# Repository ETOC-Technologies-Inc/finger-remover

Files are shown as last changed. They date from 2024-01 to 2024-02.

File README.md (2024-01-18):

# finger-remover
Tool for cutting velcro - our latest and greatest in finger removing technology

Pretty simple hardware wise (complete lies), you only need a few other (lie) parts apart from a few (lie) the 3D printed parts:
* Arduino Leonardo
* Two MG995 or One MG995 and One DS3218MG
* One Encoder without a button (i used KLS4-EC1101-5A-F20) and one Encoder module with a button (like whatever adafruit sells)
* 

# TODO/Issues

1) Fix feeding issues, oh yeah the velcro is not feeding properly rn :)

2) Add a casing for electronics, it would be nice to not hold the mess of wires in my hands

3) Make a PCB hat for the arduino its based on, and maybe add an proper LDO to it, the wires are a fucking mess and i hate them

4) Make the servo mounts fit the servos a bit less tight? They are almost impossible to slot into the mounts without a hammer rn

# Contributions

Open an issue in this repo if you see something wrong, open an MR if you think you have a fix for it, other than that pretty much anything that comlies with the license is fine.

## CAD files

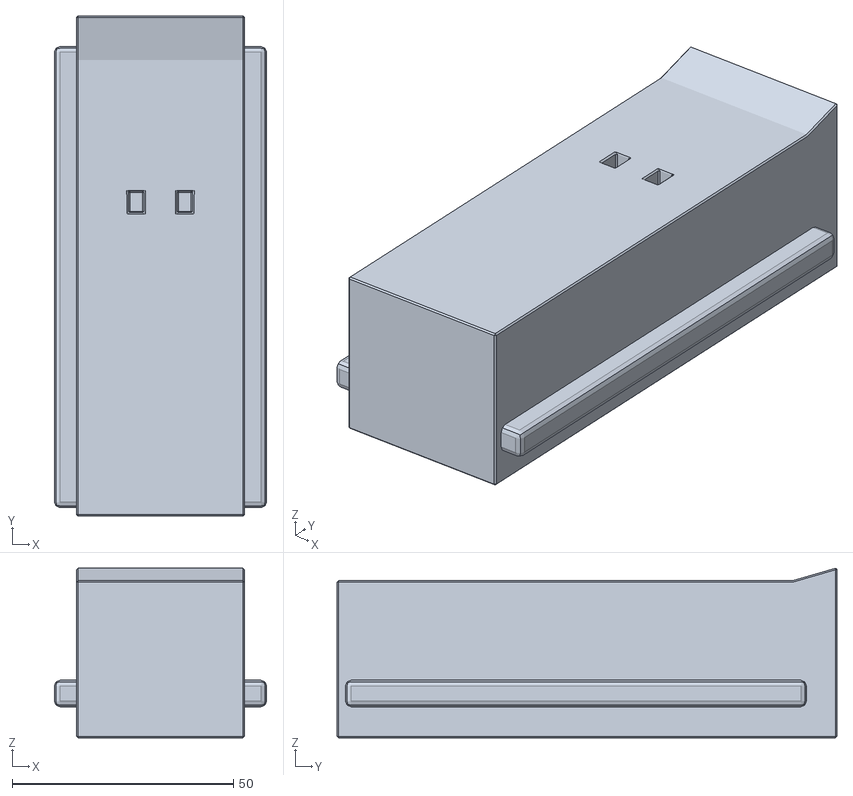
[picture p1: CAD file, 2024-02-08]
hw/main-surface.stl
48.0 x 113.0 x 38.3

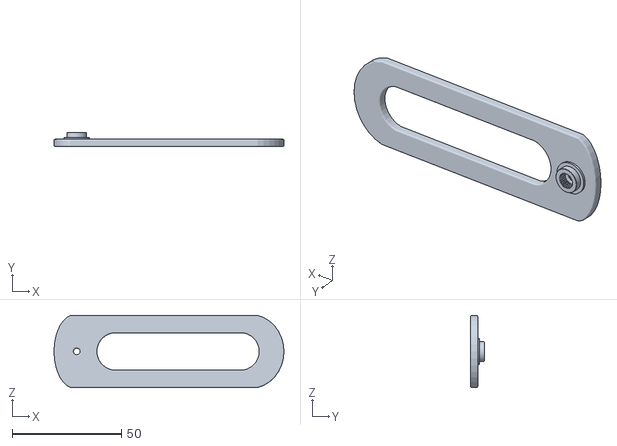
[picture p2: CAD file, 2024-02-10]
hw/sissor-cam.stl
105.3 x 6.35 x 33.1

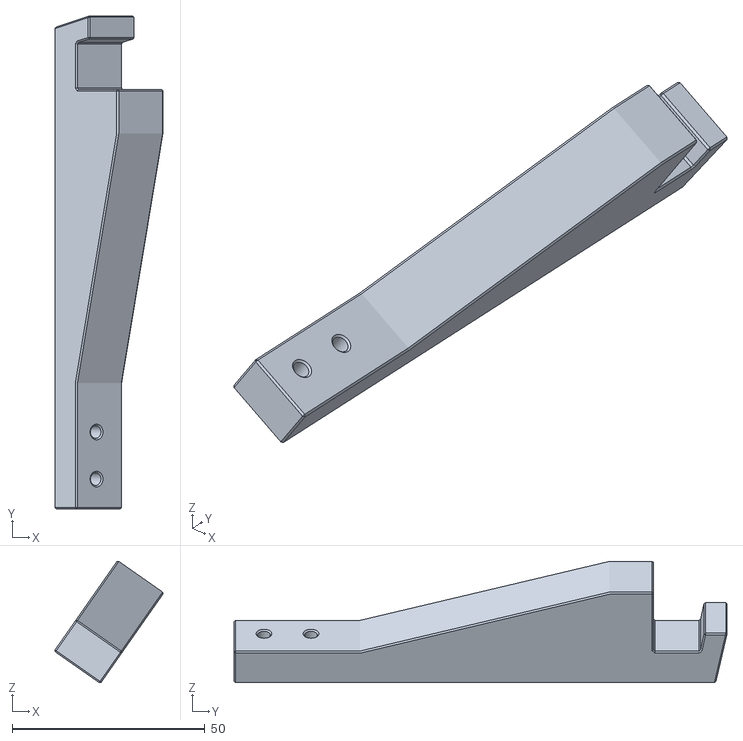
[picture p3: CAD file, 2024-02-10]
hw/sissor-holder-beam.stl
28.0 x 127.9 x 31.5

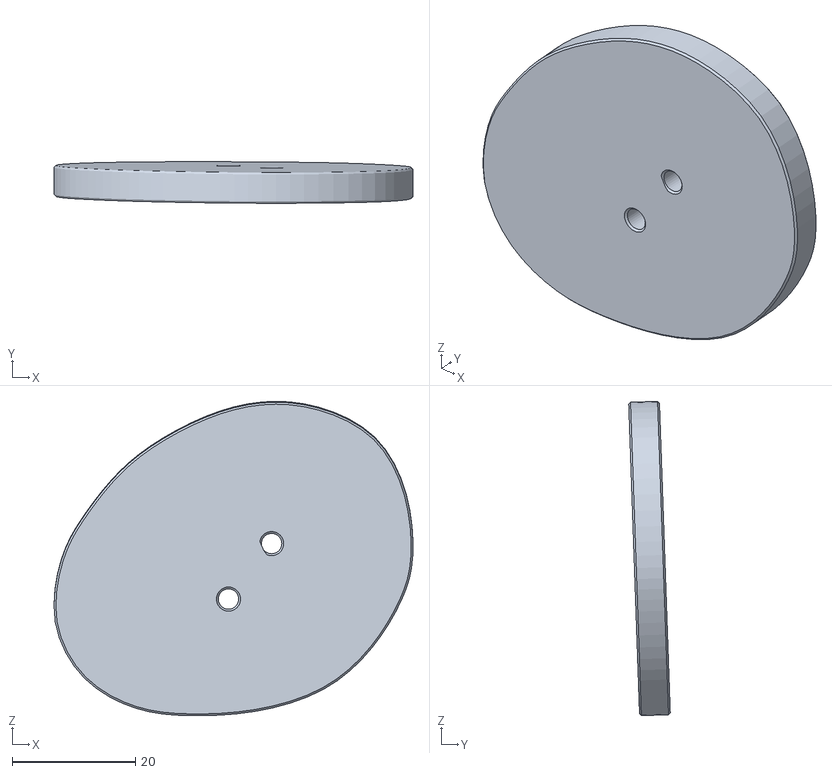
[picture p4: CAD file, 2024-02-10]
hw/sissor-holder-top.stl
58.3 x 6.75 x 51.0

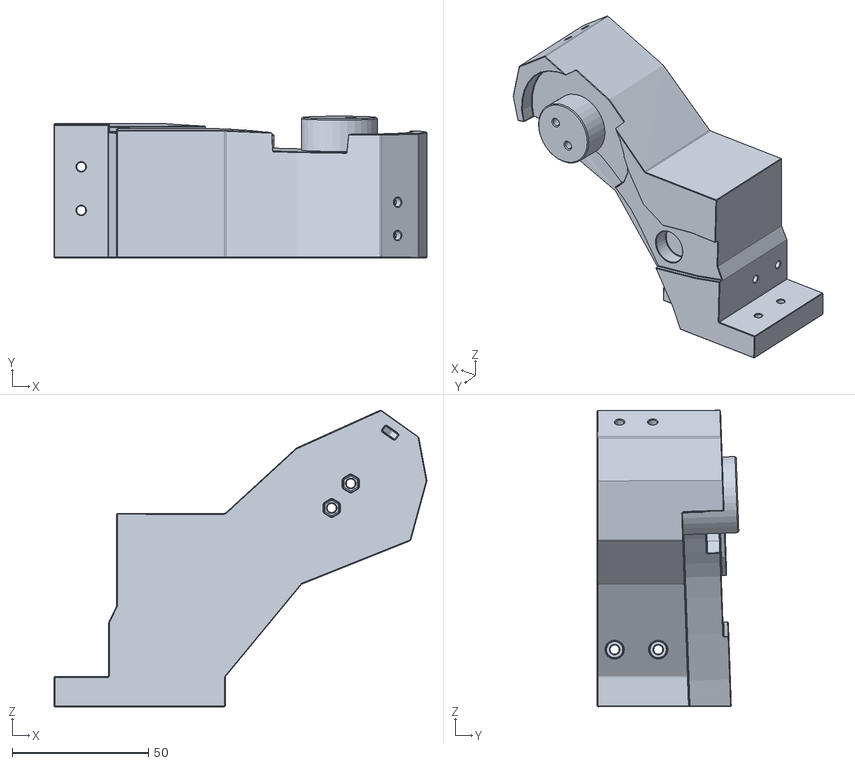
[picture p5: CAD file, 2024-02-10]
hw/sissor-holder.stl
137.0 x 52.0 x 108.9

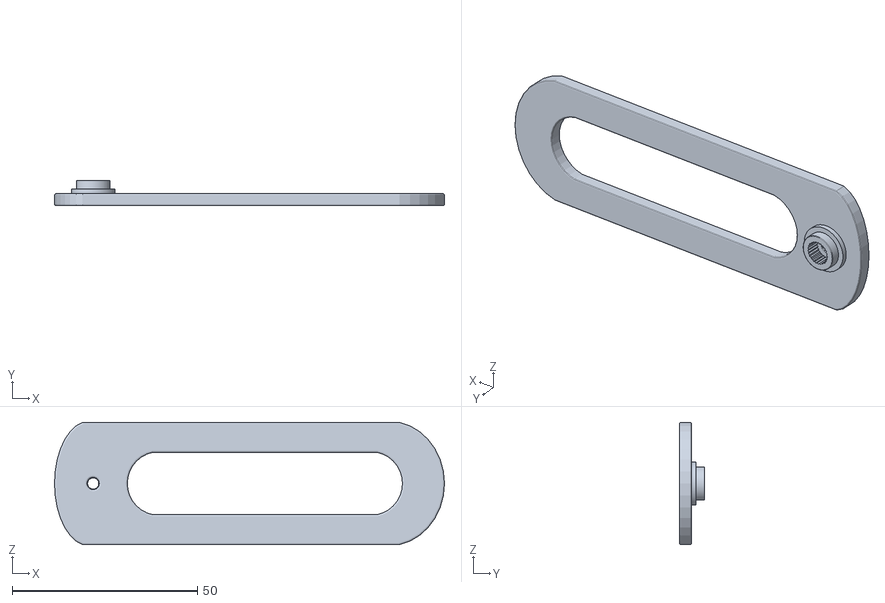
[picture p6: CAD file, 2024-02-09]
hw/sissor-servo-cam.stl
105.3 x 6.86 x 33.1

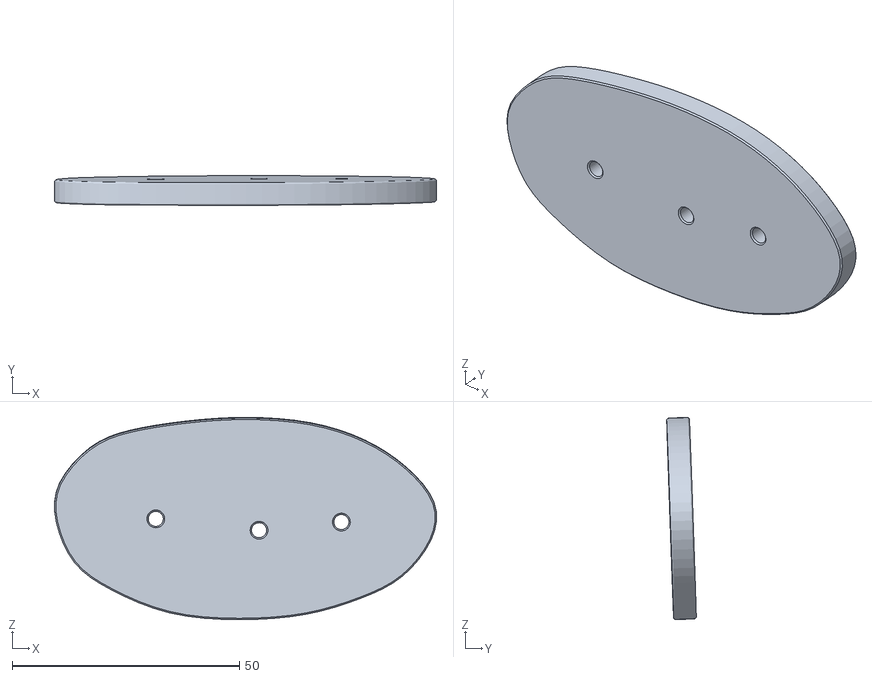
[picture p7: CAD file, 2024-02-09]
hw/sissor-cam-top.stl
84.0 x 6.52 x 44.5

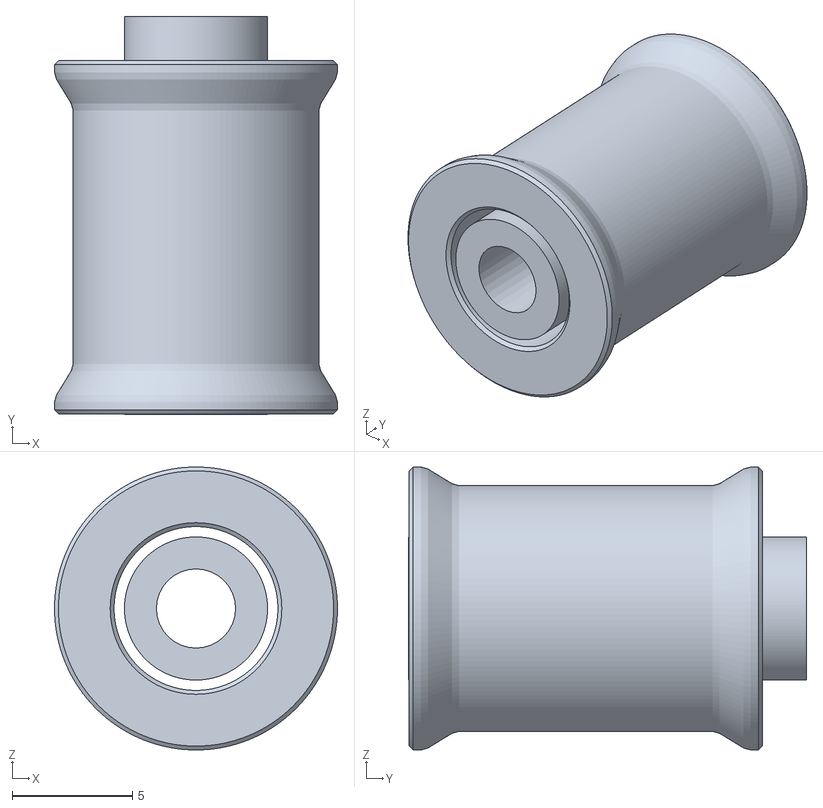
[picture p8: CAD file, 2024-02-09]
hw/sissor-cam-roller.stl
11.8 x 16.6 x 11.8

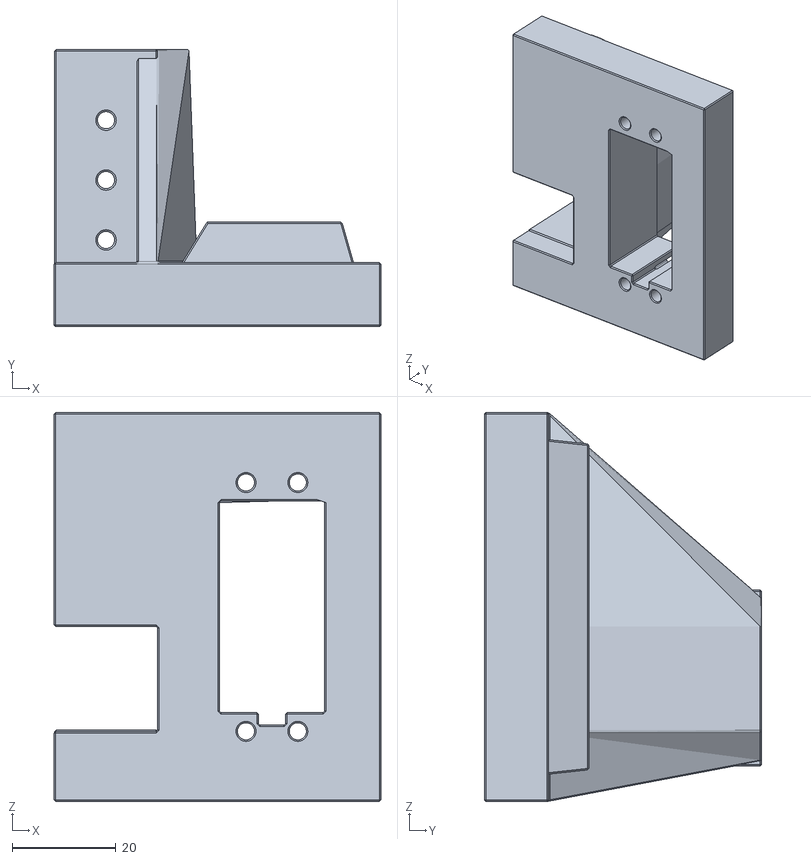
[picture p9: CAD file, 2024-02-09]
hw/servo-braket.stl
63.0 x 53.5 x 75.0

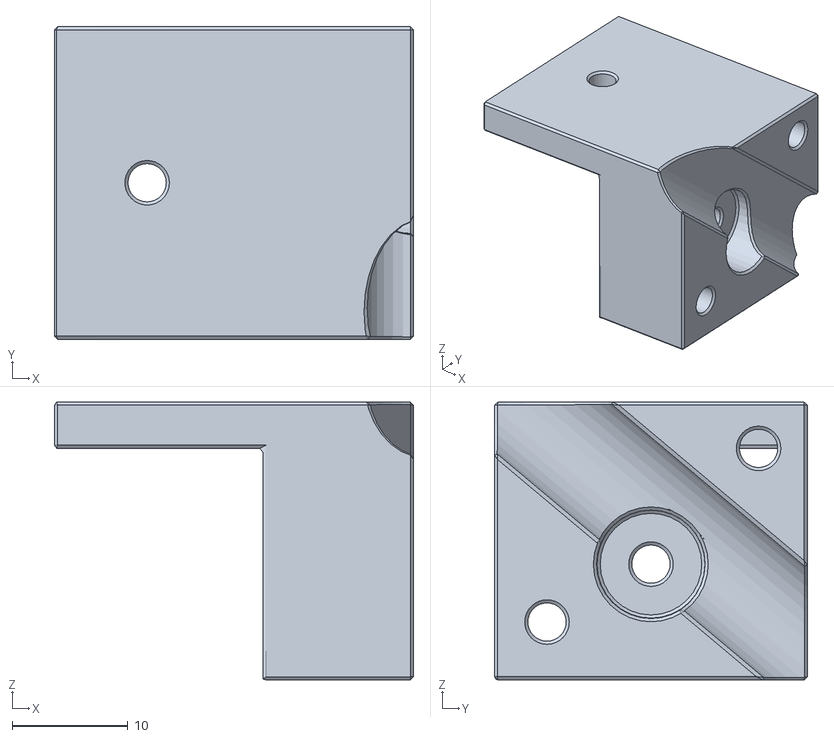
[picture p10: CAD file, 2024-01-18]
hw/spool-holder-mount.stl
31.0 x 27.0 x 24.0

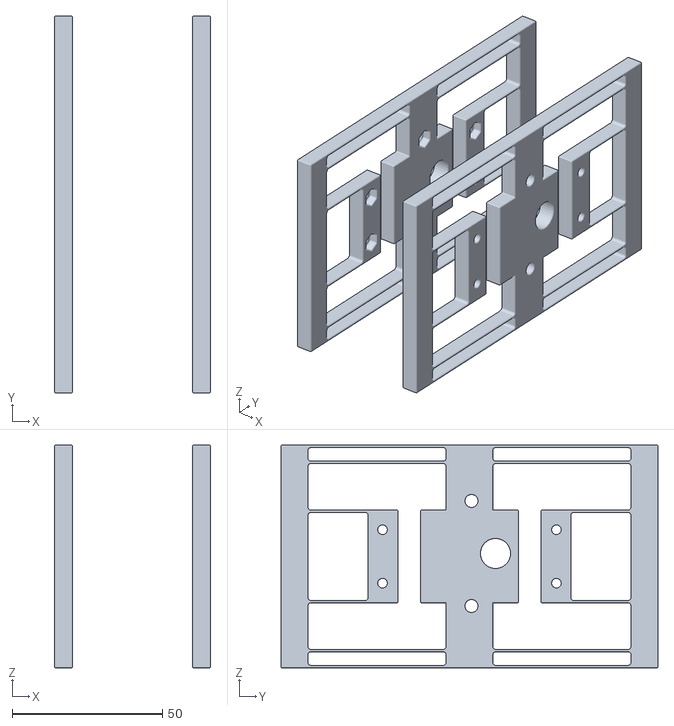
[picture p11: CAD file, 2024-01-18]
hw/compliant-mech.stl
52.0 x 125.6 x 74.1

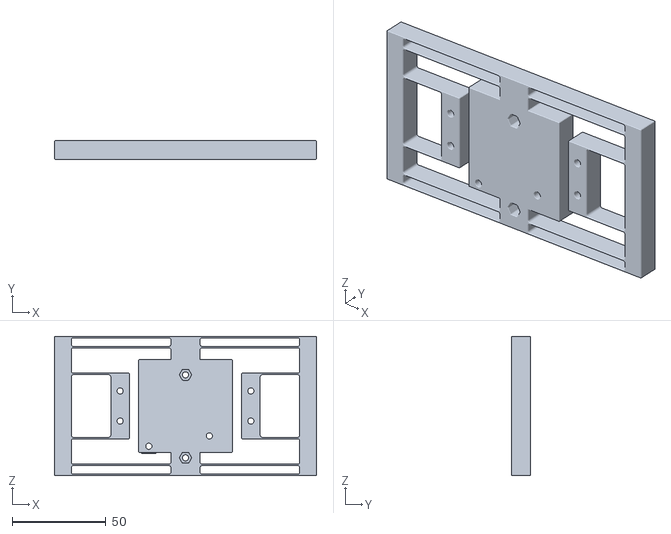
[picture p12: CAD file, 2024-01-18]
hw/compliant-mech2.stl
139.6 x 10.0 x 74.1

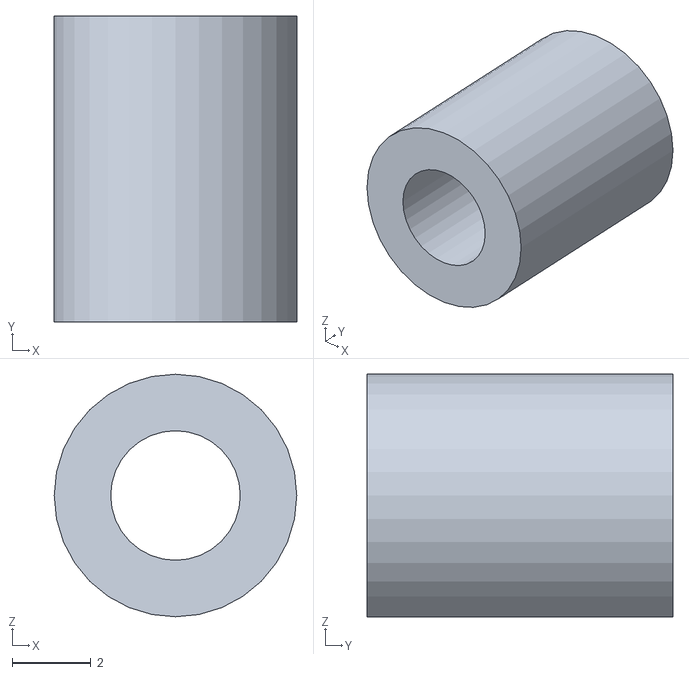
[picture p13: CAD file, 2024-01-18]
hw/cam-pullie-shaft.stl
6.18 x 7.79 x 6.18

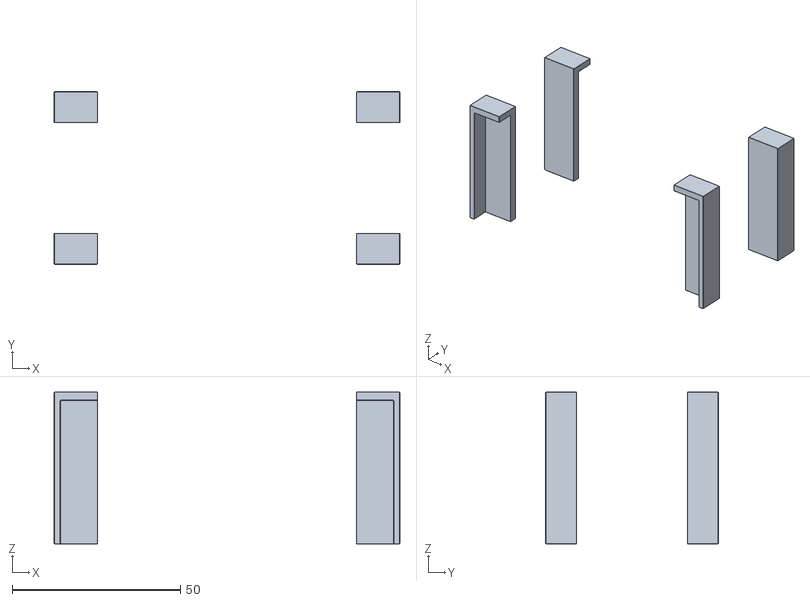
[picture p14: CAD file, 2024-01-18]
hw/feeder-shim.stl
102.9 x 51.3 x 45.1

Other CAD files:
hw/width-guide.stl
hw/top_passive.stl
hw/spool-holder-clamp.stl
hw/blade-cam-plate.stl
hw/blade-holder.stl
hw/cam-pullie.stl
hw/cam.stl
hw/cam2.stl
hw/cap-fat.stl
hw/cap-slim.stl
hw/compliant-feeder-encoder-holder.stl
hw/compliant-feeder.stl
hw/compliant-holder.stl
hw/compliant-mech3.stl
hw/finger-remover.blend
hw/guide-mod1.stl
hw/guide-mod2.stl
hw/guide-mod3.stl
hw/guide-surface.stl
hw/holder-plate.stl
hw/manual-holler-compliant-spring.stl
hw/manual-holler-guide.stl
hw/manual-holler-nail-cap.stl
hw/nail-cam-plate.stl
hw/nail-cap.stl
hw/nail-holder.stl
hw/passive-rail.stl
hw/passive-rail2.stl
hw/roller.stl
hw/roller_pin.stl
hw/servo-braket2.stl
hw/servo_horn.stl
hw/spool-holder.stl

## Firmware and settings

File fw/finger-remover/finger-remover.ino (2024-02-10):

// SPDX-License-Identifier: GPL-2.0-only

#define FEEDER_PIN 6
#define CUTTER_PIN 4
#define HOLLER_PIN 5

#define FEEDER_ENC_A 1
#define FEEDER_ENC_B 0

#define INPUT_ENC_SW 7
#define INPUT_ENC_A 2
#define INPUT_ENC_B 3

#define TFT_DISP_DC 8
#define TFT_DISP_RESET 9
#define TFT_DISP_CS 10


#define CUTTER_OPEN 110
#define CUTTER_CLOSED 180
#define HOLLER_OPEN 0
#define HOLLER_CLOSED 180


#define FEEDER_CENTER 1500
#define FEEDER_FEED_SPEED 100
#define FEEDER_TO_HOLLER_OFFSET 45.85f // in mm, hardware set, cannot be changed

// persistent memory addresses
#define FEEDER_CENTOFF_ADDR 0
#define FEEDER_STEPTIME_ADDR 32
#define FEEDER_MM_PER_STEP_ADDR 64
#define HOLE_OFFSET_ADDR 128

#define M_PI 3.14159265359f

#include <Servo.h>
#include <Encoder.h>
#include <EEPROM.h>

#include <TFT.h> // Hardware-specific library
#include <SPI.h>

Servo g_feeder;
Servo g_cutter;
Servo g_holler;

// enc handlers
Encoder g_feeder_enc(FEEDER_ENC_A, FEEDER_ENC_B);
Encoder g_input_enc(INPUT_ENC_A, INPUT_ENC_B);

// screen
TFT g_screen = TFT(TFT_DISP_CS, TFT_DISP_DC, TFT_DISP_RESET);

// menu states
enum class EMenu: uint8_t {
	Main = 0,
	CalibrateHalfStep,
	CalibrateFeederCenter,
	SetFeederMMPerStep,
	CalibrateFeederMMPerStep,
	CalibrateFeederByRoller,
	SetHoleOffset,
	Control,
	ControlFeeder,
	StartSetLen,
	StartSetNum,
	Cutting
};

EMenu curr_menu = EMenu::Main;

// op states
float target_len = 0.0f;
uint16_t target_rep = 0;
float cutter_manual_move_target = 0.0f;
bool g_button_flag = false;

// persistency
int16_t g_feeder_center_offset = 0;
uint32_t g_time_per_enc_step = 0;
float g_feeder_mm_per_step = 1.0f;
float g_hole_offset_mm = 0.0f;

void setup() {
	g_cutter.attach(CUTTER_PIN);
	g_holler.attach(HOLLER_PIN);

	g_cutter.write(CUTTER_OPEN);
	g_holler.write(HOLLER_OPEN);

	pinMode(INPUT_ENC_SW, INPUT_PULLUP);

	g_screen.begin();
	g_screen.background(0,0,0);
	g_screen.setTextSize(3);

	// persistency
	EEPROM.get(FEEDER_CENTOFF_ADDR, g_feeder_center_offset);
	g_feeder.attach(FEEDER_PIN);
	g_feeder.writeMicroseconds(FEEDER_CENTER + g_feeder_center_offset);
	EEPROM.get(FEEDER_STEPTIME_ADDR, g_time_per_enc_step);
	EEPROM.get(FEEDER_MM_PER_STEP_ADDR, g_feeder_mm_per_step);
	EEPROM.get(HOLE_OFFSET_ADDR, g_hole_offset_mm);

	Serial.begin(115200);
}

void calibrateStepTime();
void performCuttingSeq();
void cycleCutter();
void cycleHoller();
void mmPerStepCalCut();
void moveToTarget(const float target, const uint32_t move_dir = 50);

String toString100xFloat(float value) {
	return String(value, 3);
}

void loop() {
	if (curr_menu == EMenu::CalibrateHalfStep) {
		calibrateStepTime();
		curr_menu = EMenu::Main;
		return;
	} else if (curr_menu == EMenu::SetHoleOffset) {
		int32_t inpt = g_input_enc.read() / 2;

		float result = static_cast<float>(abs(inpt)) * g_feeder_mm_per_step;

		String text = toString100xFloat(result) + String("mm");

		g_screen.stroke(255, 255, 255);
		g_screen.noFill();

		g_screen.textWrap(text.c_str(), 5, 20);

		if (!digitalRead(INPUT_ENC_SW) && !g_button_flag) {
			g_button_flag = true;
		} else if (digitalRead(INPUT_ENC_SW) && g_button_flag) {
			g_button_flag = false;
			g_hole_offset_mm = result;
			EEPROM.put(HOLE_OFFSET_ADDR, g_hole_offset_mm);
			curr_menu = EMenu::Main;
			g_input_enc.readAndReset();
		}

		delay(100);
		g_screen.stroke(0,0,0);
		g_screen.textWrap(text.c_str(), 5, 20);

		return;
	} else if (curr_menu == EMenu::CalibrateFeederByRoller) {
		int inpt = g_input_enc.read() / 2;

		float result = static_cast<float>(abs(inpt)) * 0.1f;

		String text = toString100xFloat(result) + String("mm");

		g_screen.stroke(255, 255, 255);
		g_screen.noFill();

		g_screen.textWrap(text.c_str(), 5, 20);

		if (!digitalRead(INPUT_ENC_SW) && !g_button_flag) {
			g_button_flag = true;
		} else if (digitalRead(INPUT_ENC_SW) && g_button_flag) {
			g_button_flag = false;
			g_feeder_mm_per_step = (result * M_PI / 15.0f / 2.0f);
			g_hole_offset_mm = 0.0f;
			EEPROM.put(FEEDER_MM_PER_STEP_ADDR, g_feeder_mm_per_step);
			EEPROM.put(HOLE_OFFSET_ADDR, g_hole_offset_mm);
			curr_menu = EMenu::Main;
			g_input_enc.readAndReset();
		}

		delay(100);
		g_screen.stroke(0,0,0);
		g_screen.textWrap(text.c_str(), 5, 20);

		return;
	} else if (curr_menu == EMenu::SetFeederMMPerStep) {
		int inpt = g_input_enc.read() / 2;

		float result = static_cast<float>(inpt) * 0.1f;
		result = g_feeder_mm_per_step - result;

		String text = toString100xFloat(result) + String("mm");

		g_screen.stroke(255, 255, 255);
		g_screen.noFill();

		g_screen.textWrap(text.c_str(), 5, 20);

		if (!digitalRead(INPUT_ENC_SW) && !g_button_flag) {
			g_button_flag = true;
		} else if (digitalRead(INPUT_ENC_SW) && g_button_flag) {
			g_button_flag = false;
			g_feeder_mm_per_step = result;
			g_hole_offset_mm = 0.0f;
			EEPROM.put(FEEDER_MM_PER_STEP_ADDR, g_feeder_mm_per_step);
			EEPROM.put(HOLE_OFFSET_ADDR, g_hole_offset_mm);
			curr_menu = EMenu::Main;
			g_input_enc.readAndReset();
		}

		delay(100);
		g_screen.stroke(0,0,0);
		g_screen.textWrap(text.c_str(), 5, 20);

		return;
	} else if (curr_menu == EMenu::CalibrateFeederMMPerStep) {
		int inpt = g_input_enc.read() / 2;

		float result = static_cast<float>(abs(inpt));

		String text = toString100xFloat(result) + String("mm");

		g_screen.stroke(255, 255, 255);
		g_screen.noFill();

		g_screen.textWrap(text.c_str(), 5, 20);

		if (!digitalRead(INPUT_ENC_SW) && !g_button_flag) {
			g_button_flag = true;
		} else if (digitalRead(INPUT_ENC_SW) && g_button_flag) {
			g_button_flag = false;
			g_feeder_mm_per_step = result / 100.0f;
			g_hole_offset_mm = 0.0f;
			EEPROM.put(FEEDER_MM_PER_STEP_ADDR, g_feeder_mm_per_step);
			EEPROM.put(HOLE_OFFSET_ADDR, g_hole_offset_mm);
			curr_menu = EMenu::Main;
			g_input_enc.readAndReset();
		}

		delay(100);
		g_screen.stroke(0,0,0);
		g_screen.textWrap(text.c_str(), 5, 20);

		return;

	} else if (curr_menu == EMenu::ControlFeeder) {
		int inpt = g_input_enc.read() / 2;

		float result = static_cast<float>(inpt) * g_feeder_mm_per_step;

		String text = toString100xFloat(result) + String("mm");

		g_screen.stroke(255, 255, 255);
		g_screen.noFill();

		g_screen.textWrap(text.c_str(), 5, 20);

		if (cutter_manual_move_target != result) {
			moveToTarget(cutter_manual_move_target-result, FEEDER_FEED_SPEED);
			cutter_manual_move_target = result;
		}

		if (!digitalRead(INPUT_ENC_SW) && !g_button_flag) {
			g_button_flag = true;
		} else if (digitalRead(INPUT_ENC_SW) && g_button_flag) {
			g_button_flag = false;

			curr_menu = EMenu::Control;
			cutter_manual_move_target = 0.0f;
			g_input_enc.readAndReset();
		}

		delay(100);
		g_screen.stroke(0,0,0);
		g_screen.textWrap(text.c_str(), 5, 20);

		return;
	} else if (curr_menu == EMenu::Control) {
		int inpt = abs(g_input_enc.read() / 2) % 4;

		String text;

		switch (inpt) {
		case 0:
			text = "move feeder";
			break;
		case 1:
			text = "cycle cutter";
			break;
		case 2:
			text = "cycle holler";
			break;
		case 3:
			text = "back";
			break;
		}

		g_screen.stroke(255, 255, 255);
		g_screen.noFill();

		g_screen.textWrap(text.c_str(), 5, 20);

		if (!digitalRead(INPUT_ENC_SW) && !g_button_flag) {
			g_button_flag = true;
		} else if (digitalRead(INPUT_ENC_SW) && g_button_flag) {
			g_button_flag = false;
			switch (inpt) {
			case 0:
				curr_menu = EMenu::ControlFeeder;
				g_input_enc.readAndReset();
				break;
			case 1:
				cycleCutter();
				break;
			case 2:
				cycleHoller();
				break;
			case 3:
				curr_menu = EMenu::Main;
				g_input_enc.readAndReset();
				break;
			}
		}

		delay(100);
		g_screen.stroke(0,0,0);
		g_screen.textWrap(text.c_str(), 5, 20);

		return;
	} else if (curr_menu == EMenu::CalibrateFeederCenter) {
		int16_t inpt = static_cast<int16_t>(g_input_enc.read() / 2);

		int16_t result = g_feeder_center_offset + inpt;

		g_feeder.writeMicroseconds(FEEDER_CENTER + result);

		String text = String(result);

		g_screen.stroke(255, 255, 255);
		g_screen.noFill();

		g_screen.textWrap(text.c_str(), 5, 20);

		if (!digitalRead(INPUT_ENC_SW) && !g_button_flag) {
			g_button_flag = true;
		} else if (digitalRead(INPUT_ENC_SW) && g_button_flag) {
			g_button_flag = false;

			g_feeder_center_offset = result;
			EEPROM.put(FEEDER_CENTOFF_ADDR, g_feeder_center_offset);

			curr_menu = EMenu::Main;
			g_input_enc.readAndReset();
		}

		delay(10);
		g_screen.stroke(0,0,0);
		g_screen.textWrap(text.c_str(), 5, 20);

		return;
	} else if (curr_menu == EMenu::StartSetLen) {
		int inpt = g_input_enc.read() / 2;

		float result = static_cast<float>(abs(inpt)) * g_feeder_mm_per_step;

		String text = toString100xFloat(result) + String("mm");

		g_screen.stroke(255, 255, 255);
		g_screen.noFill();

		g_screen.textWrap(text.c_str(), 5, 20);

		if (!digitalRead(INPUT_ENC_SW) && !g_button_flag) {
			g_button_flag = true;
		} else if (digitalRead(INPUT_ENC_SW) && g_button_flag) {
			g_button_flag = false;
			target_len = result;
			curr_menu = EMenu::StartSetNum;
			g_input_enc.readAndReset();
		}

		delay(100);
		g_screen.stroke(0,0,0);
		g_screen.textWrap(text.c_str(), 5, 20);

		return;
	} else if (curr_menu == EMenu::StartSetNum) {
		int inpt = g_input_enc.read() / 2;

		uint16_t result = abs(inpt);

		String text = String("x") + String(result);

		g_screen.stroke(255, 255, 255);
		g_screen.noFill();

		g_screen.textWrap(text.c_str(), 5, 20);

		if (!digitalRead(INPUT_ENC_SW) && !g_button_flag) {
			g_button_flag = true;
		} else if (digitalRead(INPUT_ENC_SW) && g_button_flag) {
			g_button_flag = false;
			target_rep = result;
			curr_menu = EMenu::Cutting;
			g_input_enc.readAndReset();
		}

		delay(100);
		g_screen.stroke(0,0,0);
		g_screen.textWrap(text.c_str(), 5, 20);

		return;
	} else if (curr_menu == EMenu::Cutting) {
		performCuttingSeq();
		curr_menu = EMenu::Main;
		return;
	} else {
		int inpt = abs(g_input_enc.read() / 2) % 8;


		String text;

		switch (inpt) {
		case 0:
			text = "start";
			break;
		case 1:
			text = "control";
			break;
		case 2:
			text = "center cal";
			break;
		case 3:
			text = "half step cal";
			break;
		case 4:
			text = "mm per step cal";
			break;
		case 5:
			text = "cal by roller";
			break;
		case 6:
			text = "set per step cal";
			break;
		case 7:
			text = "set hole offset";
			break;
		}

		g_screen.stroke(255, 255, 255);
		g_screen.noFill();

		g_screen.textWrap(text.c_str(), 5, 20);

		if (!digitalRead(INPUT_ENC_SW) && !g_button_flag) {
			g_button_flag = true;
		} else if (digitalRead(INPUT_ENC_SW) && g_button_flag) {
			g_button_flag = false;
			switch (inpt) {
			case 0:
				curr_menu = EMenu::StartSetLen;
				break;
			case 1:
				curr_menu = EMenu::Control;
				break;
			case 2:
				curr_menu = EMenu::CalibrateFeederCenter;
				break;
			case 3:
				curr_menu = EMenu::CalibrateHalfStep;
				break;
			case 4:
				curr_menu = EMenu::CalibrateFeederMMPerStep;
				mmPerStepCalCut();
				break;
			case 5:
				curr_menu = EMenu::CalibrateFeederByRoller;
				break;
			case 6:
				curr_menu = EMenu::SetFeederMMPerStep;
				break;
			case 7:
				curr_menu = EMenu::SetHoleOffset;
				break;
			}
			g_input_enc.readAndReset();
		}

		delay(100);
		g_screen.stroke(0,0,0);
		g_screen.textWrap(text.c_str(), 5, 20);

		return;
	}

	delay(500);
}


void calibrateStepTime() {
	// make sure we are at the edge of a step rn
	moveToTarget(g_feeder_mm_per_step, FEEDER_FEED_SPEED);

	uint32_t avrg = 0;

	for (int i=0; i < 10; i++) {
		// time moving one step
		uint32_t start = millis();
		moveToTarget(g_feeder_mm_per_step, FEEDER_FEED_SPEED);
		uint32_t diff = millis() - start;
		avrg += diff;

		// do same thing but in the other direction
		start = millis();
		moveToTarget(-g_feeder_mm_per_step, FEEDER_FEED_SPEED);
		diff = millis() - start;
		avrg += diff;
	}

	// calculate and save step time
	g_time_per_enc_step = avrg / 20;
	EEPROM.put(FEEDER_STEPTIME_ADDR, g_time_per_enc_step);
}

void cycleCutter() {
	// g_holler.write(60);
	// delay(300);
	g_cutter.write(CUTTER_CLOSED);
	delay(1000);
	g_cutter.write(CUTTER_OPEN);
	delay(600);
	// g_holler.write(180);
	// delay(700);
}

void cycleHoller() {
	g_holler.write(HOLLER_CLOSED);
	delay(1000);
	g_holler.write(HOLLER_OPEN);
	delay(1000);
}

void moveToTarget(const float target, const uint32_t move_dir = 50) {
	int32_t move_dir2 = (target > 0) ? static_cast<int32_t>(move_dir) : -static_cast<int32_t>(move_dir);
	float target2 = abs(target);
	g_feeder_enc.readAndReset();
	while ((target2 - (static_cast<float>(abs(g_feeder_enc.read() / 2)) * g_feeder_mm_per_step)) > 0) {
		// Serial.println(target2);
		// Serial.println((abs(g_feeder_enc.read() / 2) * g_feeder_mm_per_step));
		g_feeder.write((FEEDER_CENTER + g_feeder_center_offset) + move_dir2);
	}
	g_feeder.write((FEEDER_CENTER + g_feeder_center_offset));
}

void mmPerStepCalCut() {
	g_feeder_enc.readAndReset();
	while (abs(g_feeder_enc.read() / 2) < 100) {
		g_feeder.write((FEEDER_CENTER + g_feeder_center_offset) + FEEDER_FEED_SPEED);
	}
	g_feeder.write((FEEDER_CENTER + g_feeder_center_offset));
	cycleCutter();
}

void performCuttingSeq() {
	for (int i=0; i<target_rep; i++) {		
		String text = String("x") + String(target_rep-i);

		g_screen.stroke(255, 255, 255);
		g_screen.noFill();

		g_screen.textWrap(text.c_str(), 5, 20);

		if (g_hole_offset_mm == 0) {
			moveToTarget(target_len, FEEDER_FEED_SPEED);
			cycleCutter();
		} else {
			// funny formula to calculate direction offset for the hole
			int32_t move_result = -static_cast<float>(FEEDER_TO_HOLLER_OFFSET - target_len + g_hole_offset_mm);
			Serial.println(move_result);
			moveToTarget(move_result, FEEDER_FEED_SPEED);
			cycleHoller();
			moveToTarget(FEEDER_TO_HOLLER_OFFSET + g_hole_offset_mm, FEEDER_FEED_SPEED);
			cycleCutter();
		}

		g_screen.stroke(0,0,0);
		g_screen.textWrap(text.c_str(), 5, 20);
	}
}

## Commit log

2024-01-18 all: First functional release
    This release includes these commits:
    * fw: Fixed cutter issues
    * hw: Added manual hole puncher
    * hw: Added spool holder
    * fw: Added encoder mm calibration
    * hw: Fixed pretty much all issues
    * hw: Potential fix for tape buckling issue
    * all: Added GPL2 license
    * fw: Fixed encoder and menu issues
    * fw: Added a potentially bad calibration option
    * fw: Encoder fixes and more menu stuff
    * fw: Cutter fixup
    * fw: Fixed compilation issues
    * fw: Added basic UI for TFT display
    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
    [blade-cam-plate.stl, blade-holder.stl, cam-pullie-shaft.stl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]
2024-01-18 fw: Fixed calibration and cutter issues
    [finger-remover.ino]
2024-01-19 fw: Added hole punching funtion
    Now users can set an offset after which the holes will be punched
2024-02-06 fw: Fixed math conversion issues
    [finger-remover.ino]
2024-02-06 hw: Prep for replacing sissors
    [finger-remover.blend, sissor-cam.stl, sissor-holder.stl]
2024-02-08 hw: More sissors prep
    [finger-remover.blend, main-surface.stl, sissor-cam.stl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]
2024-02-09 hw: Almost done with the new sissors cutter
    [finger-remover.blend, servo-braket.stl, sissor-cam-roller.stl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]
2024-02-10 fw: Reset hole offset after roller calibration
    [finger-remover.ino]
2024-02-10 hw: Added final touches to the sissor holder
    [finger-remover.blend, sissor-holder-beam.stl, sissor-holder-top.stl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]
2024-02-10 hw: Fixed cam mount
    [finger-remover.blend, sissor-cam.stl]
2024-02-10 fw: Adapted to new holler servo orientation
